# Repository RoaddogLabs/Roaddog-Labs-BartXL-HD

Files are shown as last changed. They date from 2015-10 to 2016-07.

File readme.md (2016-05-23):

## Roaddog Labs Bart Pro XL
## 
This is the Roaddog Bart XL 3D printer. This machine is a larger build
based on a mashup implemented from several designs including original
designs.  

####This machine is available in two variants

#####Bart Pro XL-LC is a lower cost version and a good upgrade platform for those with a Prusa i3 or Rework i3 variant to upgrade to a better frame and larger build area.  The LC variant uses M8 X and Z smooth rods and M5 threaded rod for the Z drive screw.  The LC uses Rework i3 printed parts.

The Bart Pro XL-LC version is frozen.  The current version is the Bart Pro XL-HD.  There will be no more work on this version but feel free to fork it and do with it as you wish.

#####Bart Pro XL-HD uses high performance lead screws, M10 precision shaft on all axis, high temp hot end suitable to 400*C, auto bed probe (bed leveling), silcone bed heater, MIC 6 precision aluminum print surface with PEI.

### This is a pre release version
### 
The current version is a pre release.  While the machine is functional
and works well, it's still very much a work in progress.  A set of pre release docs are at http://roaddoglabs.io/wiki/Roaddog_Labs_Bart_Pro_XL

Pull requests are welcome and encouraged.

#### Roaddog Labs Bart Pro XL-HD Specs ####

| Feature | Bart Pro XL-HD |
|---|---|
| Base and Frame | Full melamine frame, printed parts, latest design for maximum stability and print speeds |
| Build Envelope | 360 mm x 240 mm x 200 mm |
| Resolution (printable layer thickness) | low res .3 mm; normal res .2 mm; hi res .1 mm; extra hi res .06 mm |
| Filament Diameter | 1.75 |
| Max Printing Temp | 248&#176; C with E3D Lite v6; 300&#176; C with E3D full v6 with thermistor, 400&#176; C with optional thermocouple |
| Compatible Materials | With E3D v6, any printable material to 400&#176; C with E3D v6 and thermocouple.  With E3D Lite v6 more than 15 types including PLA, ABS, Laywoo-D, HIPS, carbon fiber reinforced PLA, flexible filament, conductive PLA |
| Nozzle Size | .4 mm standard, user upgradable to a variety of sizes |
| Heated Bed | Polyimide heater, 24 volt with aluminum heat spreader |
| Print Surface |0.125" 6061-T6 aluminum |
| Extruder | Bart Direct Drive MK7, low profile, reduced weight and mass, optional E3D Titan or Bondtech QR extruder |
| Bed Tilt Compensation | Belt tilt compensation, also called auto bed leveling or tramming via an inductive sensor |
|Electronics | Mini Rambo configured for Bart Pro XL with Marlin firmware |
| Power Supply | 24 volts, 400 watts compact form factor |
| X Axis Motion | GT2 belt and pulley;  10 mm precision  bearings and chromed, hardened rods |
| Y Axis Motion | GT2 belt and pulley;  10 mm precision  bearings and chromed, hardened rods |
| Z Axis Motion | TR8 precision lead screw and nut; 10 mm precision bearings and chromed, hardened rods |
| Average Speeds | 100 mm/s (stock extruder, perimeters based on average tune) |
| Machine Footprint | 512 mm x 470 mm x 400 mm |
| Display/SD Card Reader | Full graphic LCD display and SD card reader for standalone operation |
| Optional Wireless and Print Server | User installed optional printing over Wifi and dedicated print server using Octoprint and a Raspberry Pi |

####License and Credits

Original designs from Roaddog Labs Ltd are released per the
Open Source Hardware Association guidelines for open source hardware at
http://www.oshwa.org/definition/.

Material specific to the Bart components and documentation that is not
derived from other sources are released under the Creative Commons
Attribution 4.0 International license.

Where applicable, the license of any derived work will be posted as
well.

The original Prusa i3 single plate files
(https://github.com/josefprusa/Prusa3) from Josef Prusa licensed under
GPL v3.

The original i3 Rework
(https://github.com/eMotion-Tech/Prusai3_EINSTEIN_Reworked) printed
parts files from eMotion-Tech are released under GPL 2.0.

The original i3 Hephestos files
(https://github.com/bq/prusa-i3-hephestos/) from bq Department of
Innovation and Robotics are licensed under Creative Commons Attribution
4.0 Sharealike International.

The Graber i3(https://github.com/sgraber/Graber) is licensed under GPL
v3.0.

The original modified i3 X idler with adjustable belt tensioner from
ramkam (http://www.thingiverse.com/thing:393870) licensed under Creative
Commons Atribution-Sharealike, no version stated.

Marlin firmware (https://github.com/MarlinFirmware/Marlin) from Erik van
der Zalm licensed under GPL, no version stated.

The original direct drive extruder for Wilson/i3
(http://www.thingiverse.com/thing:501755) from mrice licensed under
Creative Commons Attribution- Share Alike license, no version stated.

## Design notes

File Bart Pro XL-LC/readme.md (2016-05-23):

## Roaddog Labs Bart Pro XL-LC
## 
This is a Roaddog Bart XL-LC 3D printer. This machine is a larger build
based on a mashup implemented from several designs including original
designs.  Original designs from Roaddog Labs Ltd are released per the
Open Source Hardware Association guidelines for open source hardware at
http://www.oshwa.org/definition/.

#####Bart Pro XL-LC is a lower cost version and a good upgrade platform for those with a Prusa i3 or Rework i3 variant to upgrade to a better frame and larger build area.  The LC variant uses M8 X and Z smooth rods and M5 threaded rod for the Z drive screw.  The LC uses Rework i3 printed parts.

This design is a legacy design and is frozen.  Feel free to fork it and add to it as you would like.

#### Roaddog Labs Bart Pro XL-LC Specs ####

| Feature | Bart Pro XL |
|---|---|
| Base and Frame | Full melamine frame, printed parts, latest design for maximum stability and print speeds |
| Build Envelope | 360 mm x 240 mm x 200 mm |
| Resolution (printable layer thickness) | low res .3 mm; normal res .2 mm; hi res .1 mm; extra hi res .06 mm |
| Filament Diameter | 1.75 |
| Max Printing Temp | 248&#176; C with E3D Lite v6; 300&#176; C with E3D full v6 with thermistor, 400&#176; C with optional thermocouple |
| Compatible Materials | With E3D v6, any printable material to 400&#176; C with E3D v6 and thermocouple.  With E3D Lite v6 more than 15 types including PLA, ABS, Laywoo-D, HIPS, carbon fiber reinforced PLA, flexible filament, conductive PLA |
| Nozzle Size | .4 mm standard, user upgradable to a variety of sizes |
| Heated Bed | Polyimide heater, 24 volt with aluminum heat spreader |
| Print Surface | 3mm borosilicate glass |
| Extruder | Bart Direct Drive MK7, low profile, reduced weight and mass |
|Electronics | Mini Rambo configured for Bart Pro XL with Marlin firmware |
| Power Supply | 24 volts, 400 watts compact form factor |
| X Axis Motion | GT2 belt and pulley;  8 mm precision  bearings and chromed, hardened rods |
| Y Axis Motion | GT2 belt and pulley;  10 mm precision  bearings and chromed, hardened rods |
| Z Axis Motion | M5 threaded rod drive screw and nut; 8 mm precision bearings and chromed, hardened rods |
| Average Speeds | 70 mm/s (stock extruder, perimeters based on average tune) |
| Machine Footprint | 512 mm x 470 mm x 400 mm |
| Display/SD Card Reader | Full graphic LCD display and SD card reader for standalone operation |
| Optional Wireless and Print Server | User installed optional printing over Wifi and dedicated print server using Octoprint and a Raspberry Pi |

####License and Credits
Material specific to the Bart components and documentation that is not
derived from other sources are released under the Creative Commons
Attribution 4.0 International license.

Where applicable, the license of any derived work will be posted as
well.

The original Prusa i3 single plate files
(https://github.com/josefprusa/Prusa3) from Josef Prusa licensed under
GPL v3.

The original i3 Rework
(https://github.com/eMotion-Tech/Prusai3_EINSTEIN_Reworked) printed
parts files from eMotion-Tech are released under GPL 2.0.

The original i3 Hephestos files
(https://github.com/bq/prusa-i3-hephestos/) from bq Department of
Innovation and Robotics are licensed under Creative Commons Attribution
4.0 Sharealike International.

The Graber i3(https://github.com/sgraber/Graber) is licensed under GPL
v3.0.

The original modified i3 X idler with adjustable belt tensioner from
ramkam (http://www.thingiverse.com/thing:393870) licensed under Creative
Commons Atribution-Sharealike, no version stated.

Marlin firmware (https://github.com/MarlinFirmware/Marlin) from Erik van
der Zalm licensed under GPL, no version stated.

The original direct drive extruder for Wilson/i3
(http://www.thingiverse.com/thing:501755) from mrice licensed under
Creative Commons Attribution- Share Alike license, no version stated.

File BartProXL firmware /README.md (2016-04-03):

### Roaddog Labs Bart Pro XL Firmware
### 
__Not for production use – use with caution!__

This fork is configured specifically for the Roaddog Labs Pro XL.  It's
currently based on Marlin 1.1.0-RC3 that was pushed 01 Dec, 2015.  This build is configured for a Mini Rambo controller using 360 mm x 240 mm print bed and Reprap Discount GLCD display

This build defaults to an induction probe in place of a mechanical Z end stop. The file [Configuration_mechanical_z.txt](./Bart_Pro_XL/Configuration_mechanical_z.txt) contains the settings for using a mechanical end stop in the A position.  To use this configuration rename the file to Configuration.h  and build the firmware.

The [original README.md](Orig_README.md) from the fork.

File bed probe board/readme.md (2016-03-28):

This is the voltage divider circuit and board layout for the Roaddog Labs Bart Pro XL.  It takes a 24 volt input and reduces the switch output to 5 volts for triggering the MCU on the printer.

This is pre release, not for production.

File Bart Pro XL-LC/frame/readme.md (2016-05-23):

## Roaddog Labs Bart Pro XL-LC
## 

Cut the following frame parts

* 2 x bart pro xl-lc side
* 2 x bart pro xl-lc z motor mount
* 2 x bart pro xl-lc z motor support
* 2 x bart pro xl-lc z top rod stop
* 2 x bart pro xl-lc y idler bearing mount
* 2 x bart pro xl-lc y belt holder

* 1 x bart pro xl-lc base 
* 1 x bart pro xl-lc print bed
* 1 x bart pro xl-lc top cross
* 1 x bart pro xl-lc y endstop bracket
* 1 x bart pro xl-lc z frame
* 1 x bart xl-lc end front
* 1 x bart xl-lc end rear

####License and Credits
Material specific to the Bart components and documentation that is not
derived from other sources are released under the Creative Commons
Attribution 4.0 International license.

Where applicable, the license of any derived work will be posted as
well.

The original Prusa i3 single plate files
(https://github.com/josefprusa/Prusa3) from Josef Prusa licensed under
GPL v3.

The original i3 Rework
(https://github.com/eMotion-Tech/Prusai3_EINSTEIN_Reworked) printed
parts files from eMotion-Tech are released under GPL 2.0.

The original i3 Hephestos files
(https://github.com/bq/prusa-i3-hephestos/) from bq Department of
Innovation and Robotics are licensed under Creative Commons Attribution
4.0 Sharealike International.

The Graber i3(https://github.com/sgraber/Graber) is licensed under GPL
v3.0.

The original modified i3 X idler with adjustable belt tensioner from
ramkam (http://www.thingiverse.com/thing:393870) licensed under Creative
Commons Atribution-Sharealike, no version stated.

Marlin firmware (https://github.com/MarlinFirmware/Marlin) from Erik van
der Zalm licensed under GPL, no version stated.

The original direct drive extruder for Wilson/i3
(http://www.thingiverse.com/thing:501755) from mrice licensed under
Creative Commons Attribution- Share Alike license, no version stated.

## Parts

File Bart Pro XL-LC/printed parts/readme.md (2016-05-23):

## Roaddog Labs Bart Pro XL-LC
## 

Print the following parts

* 1 x bart pro xl-lc y motor mount
* 8 x bart pro xl-lc Y bearing mount
* 3 x bart pro xl-lc y clip
* 1 x bart pro xl-lc y end stop bracket

* 1 x bart pro xl-lc X motor end
* 1 x bart pro xl-lc X idler end
* 1 x bart pro xl-lc x belt  idler  
* 1 x bart pro xl-lc x endstop bracket
* 1 x bart pro xl-lc x endstop block
* 1 x bart pro xl-lc x carriage

* 1 x bart pro xl-lc z endstop bracket
* 1 x bart pro xl-lc extruder
* 1 x bart pro xl-lc extruder fan duct

####License and Credits
Material specific to the Bart components and documentation that is not
derived from other sources are released under the Creative Commons
Attribution 4.0 International license.

Where applicable, the license of any derived work will be posted as
well.

The original Prusa i3 single plate files
(https://github.com/josefprusa/Prusa3) from Josef Prusa licensed under
GPL v3.

The original i3 Rework
(https://github.com/eMotion-Tech/Prusai3_EINSTEIN_Reworked) printed
parts files from eMotion-Tech are released under GPL 2.0.

The original i3 Hephestos files
(https://github.com/bq/prusa-i3-hephestos/) from bq Department of
Innovation and Robotics are licensed under Creative Commons Attribution
4.0 Sharealike International.

The Graber i3(https://github.com/sgraber/Graber) is licensed under GPL
v3.0.

The original modified i3 X idler with adjustable belt tensioner from
ramkam (http://www.thingiverse.com/thing:393870) licensed under Creative
Commons Atribution-Sharealike, no version stated.

Marlin firmware (https://github.com/MarlinFirmware/Marlin) from Erik van
der Zalm licensed under GPL, no version stated.

The original direct drive extruder for Wilson/i3
(http://www.thingiverse.com/thing:501755) from mrice licensed under
Creative Commons Attribution- Share Alike license, no version stated.

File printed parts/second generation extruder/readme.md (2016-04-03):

Roaddog Labs Ltd Bart Pro XL 2nd Gen Extruder

This is a prototype 2nd generation extruder.  

Updates include 

provisions for the push connector in the E3D hot end

two screw JHead style mount

This is still experimental pull requests and suggestions are encouraged.

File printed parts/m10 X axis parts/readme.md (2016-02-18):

Roaddog Labs Ltd Bart Pro XL LM10UU X axis

This is a prototype X axis using LM10UU bearings and M10 shafts.  This is still experimental pull requests and suggestions are encouraged.

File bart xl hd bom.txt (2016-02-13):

**** not released for production ****
**** copied from Bart, needs audit ****

Bill of Materials
Roaddog Labs Ltd Bart XL HD
file released under Creative Commons
Attribution 4.0 International license.

Frame

2 x 24" x18" 1/4" melamine, black or white, two sides laminated

Rods

2 x M5-.8 x 300 mm threaded rod, Z axis lead screws

2 x M8 x 318 mm smooth rod, (320 mm will work also)

2 x M8 x 368 mm smooth rod 

2 x M10 x 511 mm smooth rod 

Bearings

4 x LM10UU linear bearings
7 x LM8UU linear bearings
3 x 624ZZ bearings

Printed Parts

4 x Y clips
1 x Y motor bracket
4 x Y bearing mounts (each mount is two pieces)

1 x X carriage
1 x x endstop block
1 x X end motor
1 x X end idler
1 x X idler

1 x extruder body 
1 x extruder idler
1 x hot end mounting clip
1 x fan duct

1 x z endstop bracket

Misc Hardware

1 x M7 hobbed drive gear, filament drive gear
2 x GT2 pulley, 20 teeth, 5 mm diameter mounting hole
2 meters GT2 belt

4 x rubber feet

2 x 3/16" ID poly tubing, 1" long each, coupler tubing 

1 x 214 x 200 borosilicate glass print bed

4 x small binder clips for glass bed

4 bed springs (get final specs)
2 extruder springs (get final specs)

Fasteners  (totals rounded up from final prototype, shcs count not exact)

50 x 6-32 square nut, frame
50 x 6-32 x 5/8" pan head machine screws, frame
4 x 6-32 x 1/2" pan head machine screws, frame
4 x #6 flat washer, frame

20 x  M3 x 10 mm shcs, motor mounts, endstop screws
25 x  M3 x 12 mm shcs, motor/Z endstop bracket mounting, feet mounting
05 x  M3 x 14 mm shcs,
05 x  M3 x 16 mm shcs,
08 x  M3 x 25 mm shcs,
06 x  M3 x 30 mm shcs, 
02 x  M3 x 35 mm shcs,
02 x  M3 x 50 mm shcs,

55 x  M3 washer
30 x  M3 hex nut
12 x  M3 nyloc nut

07 x  M4 x 20 shcs extruder mount, extruder idler
01 x  M4 x 30 shcs Y idler bearing

06 x  M4 hex nut
10 x  M4 flat washer
03 x  M4 nyloc nut

02 x  M5 nut

4 x nylon spacers (snap fit does not fit iduino/Arduino pcb mounting hole)

Electronics

1 x Mini Rambo control board

1 x 40x40x10 12 volt axial fan

5 x NEMA 17 stepper motors, recommend 76 oz/in holding torque

1 x 400 watt, 24 volt PSU

1 x kapton tape heating pad

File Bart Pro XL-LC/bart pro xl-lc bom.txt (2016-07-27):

Bill of Materials
Roaddog Labs Ltd Bart Pro XL-LC
file released under Creative Commons
Attribution 4.0 International license.

Frame

2 x 24" x18" 1/4" melamine, two sides laminated

Rods

2 x M5-.8 x 300 mm threaded rod, Z axis drive screws

2 x M8 x 318 mm smooth rod

2 x M8 x 370 mm smooth rod 

2 x M10 x 511 mm smooth rod 

Bearings

4 x LM10UU linear bearings
8 x LM8UU linear bearings
3 x 624ZZ bearings

Printed Parts

2 x Y clips
1 x Y clip/end stop bracket
1 x Y motor bracket
4 x Y bearing mounts (each mount is two pieces)

1 x X carriage
1 x x endstop block
1 x X end motor
1 x X end idler
1 x X idler

1 x extruder body 
1 x extruder idler
1 x hot end mounting clip
1 x fan duct

1 x z endstop bracket

Misc Hardware

1 x M7 hobbed drive gear, filament drive gear
2 x GT2 pulley, 20 teeth, 5 mm diameter mounting hole
2 meters GT2 belt

4 x rubber feet

2 x 3/16" ID poly tubing, 1" long each, coupler tubing 

1 x 214 x 200 borosilicate glass print bed

4 x small binder clips for glass bed

4 x bed springs (get final specs)
2 x extruder springs (get final specs)

1 x aluminum print bed sheet .125 thick, 360 mm x 240 mm 6061-T6 

1 x borosilicate glass, 3 mm thick 360 mm x 240 mm 

Fasteners 

50 x 6-32 square nut, frame
50 x 6-32 x 5/8" pan head machine screws, frame
4 x 6-32 x 1/2" pan head machine screws, frame
4 x #6 flat washer, frame

20 x  M3 x 10 mm shcs, motor mounts, endstop screws
25 x  M3 x 12 mm shcs, motor/Z endstop bracket mounting, feet mounting
05 x  M3 x 14 mm shcs,
05 x  M3 x 16 mm shcs,
08 x  M3 x 25 mm shcs,
06 x  M3 x 30 mm shcs, 
02 x  M3 x 35 mm shcs,
02 x  M3 x 50 mm shcs,

55 x  M3 washer
30 x  M3 hex nut
12 x  M3 nyloc nut

07 x  M4 x 20 shcs extruder mount, extruder idler
01 x  M4 x 30 shcs Y idler bearing

06 x  M4 hex nut
10 x  M4 flat washer
03 x  M4 nyloc nut

02 x  M5 nut

4 x nylon spacers (snap fit does not fit iduino/Arduino pcb mounting hole)

Electronics

1 x Mini Rambo control board

1 x E3D v6 hot end kit

1 x 40x40x10 24 volt axial fan

5 x NEMA 17 stepper motors, recommend 76 oz/in holding torque

1 x 400 watt, 24 volt PSU

1 x kapton tape heating pad

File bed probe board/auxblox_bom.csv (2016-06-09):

CN1,CN2 | S1011EC-40-ND | 2
R1 | 985-1300-1-ND | 1
R2 | 985-1311-1-ND | 1

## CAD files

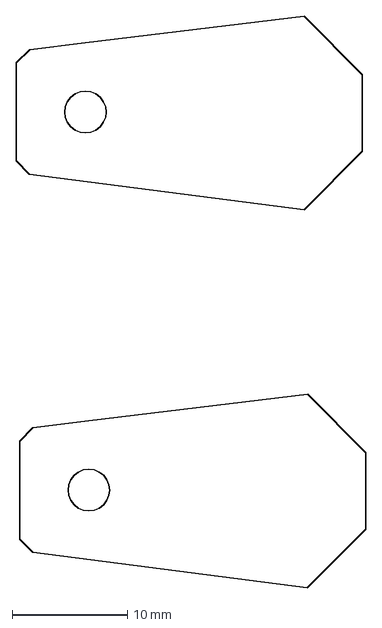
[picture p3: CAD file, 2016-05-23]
Bart Pro XL-LC/frame/bart pro xl-lc z top rod stop.dxf
30.3 x 49.6 mm

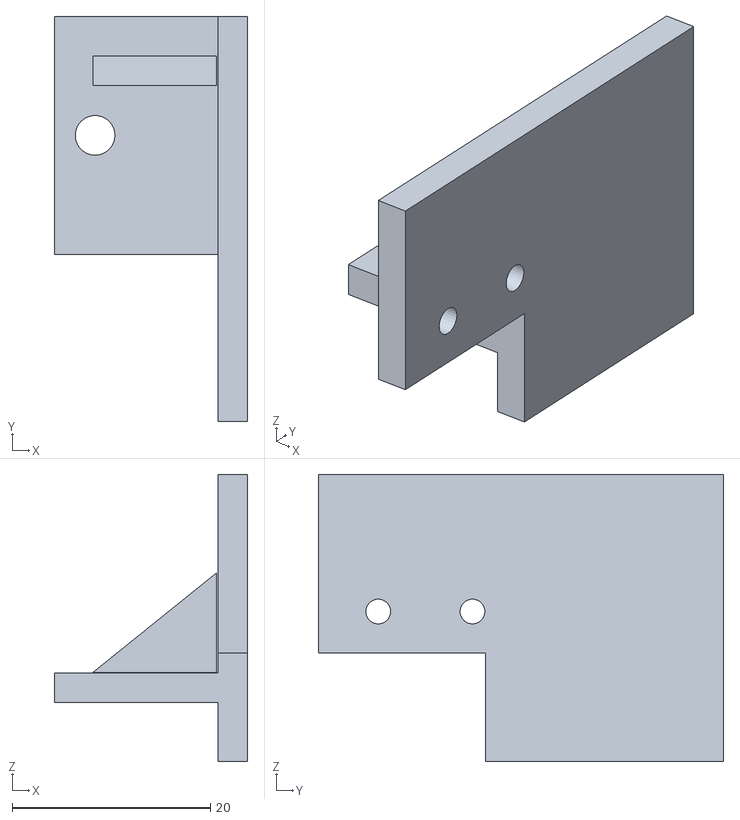
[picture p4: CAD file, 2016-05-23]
Bart Pro XL-LC/printed parts/bart pro xl-lc y end stop bracket.stl
19.5 x 40.9 x 28.9

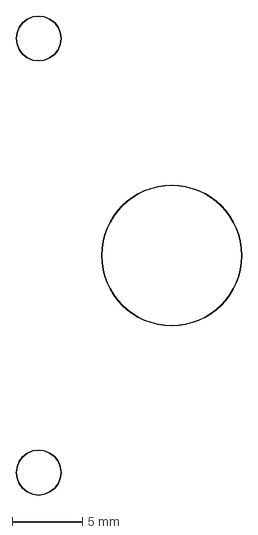
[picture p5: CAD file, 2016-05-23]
frame/bart pro xl m10 bottom Z rod guide spacing.dxf
16.1 x 34.2 mm

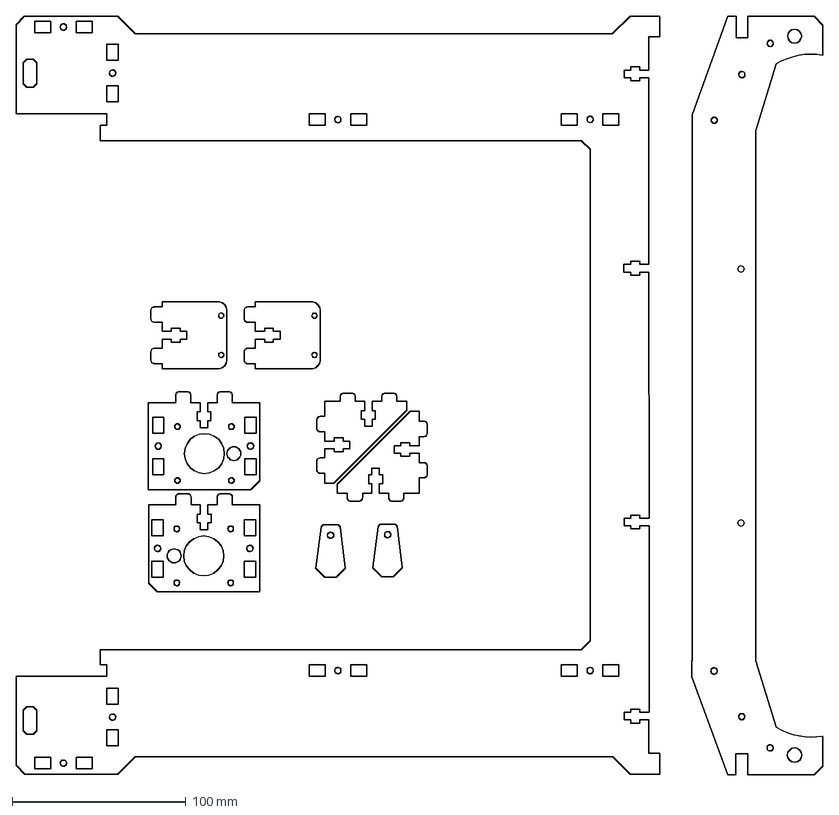
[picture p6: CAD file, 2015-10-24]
frame/v1 frame parts/bart xl one piece top cross and frame v2.dxf
463.9 x 436.3 mm

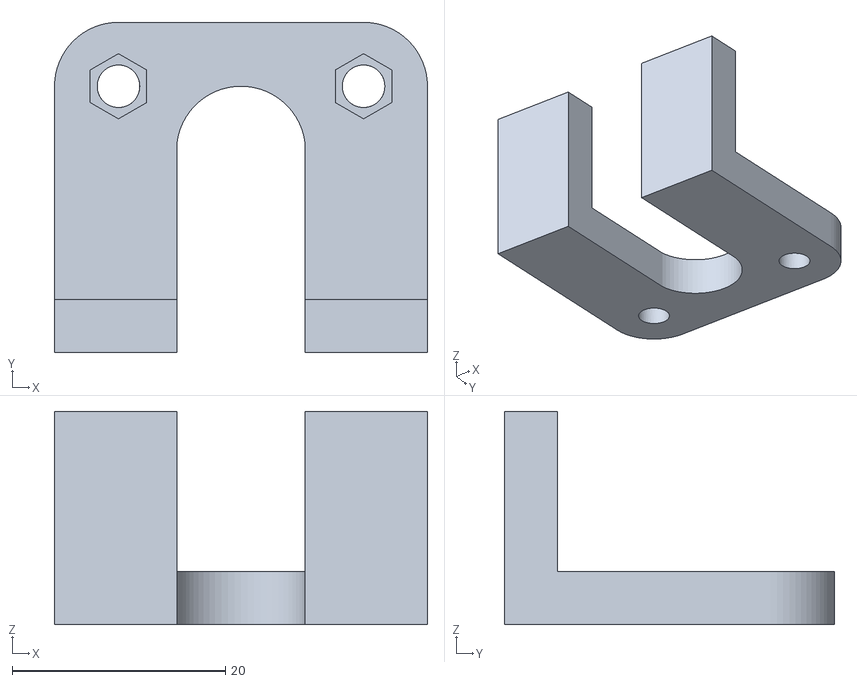
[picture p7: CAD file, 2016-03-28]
printed parts/bart pro xl bed probe bracket.stl
35.0 x 31.0 x 20.0

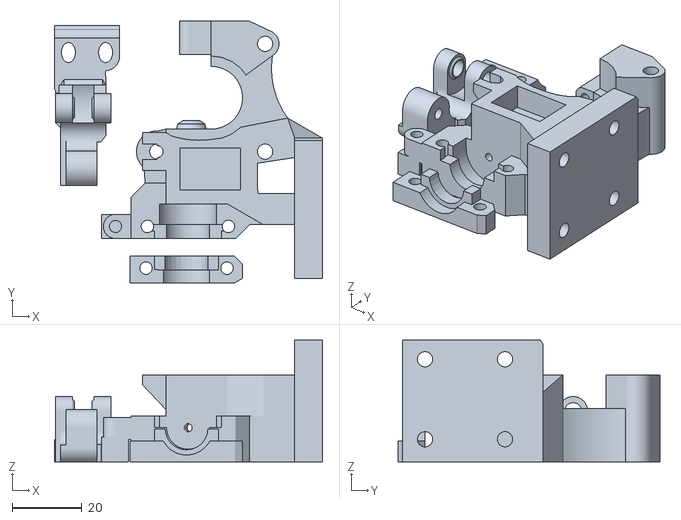
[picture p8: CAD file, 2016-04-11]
printed parts/dual extruder/extruder motor on right.stl
77.1 x 75.2 x 35.0

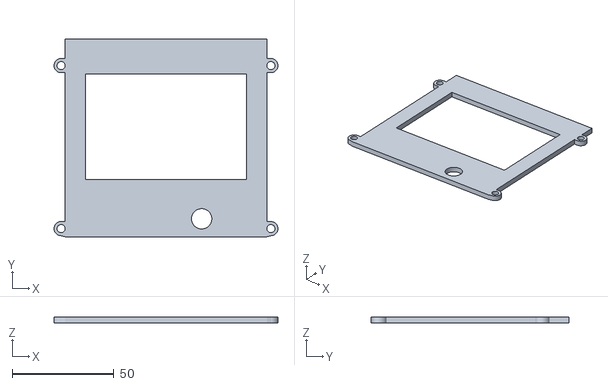
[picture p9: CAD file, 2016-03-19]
printed parts/glcd case/bart pro xl glcd case face.stl
110.0 x 97.0 x 3.00

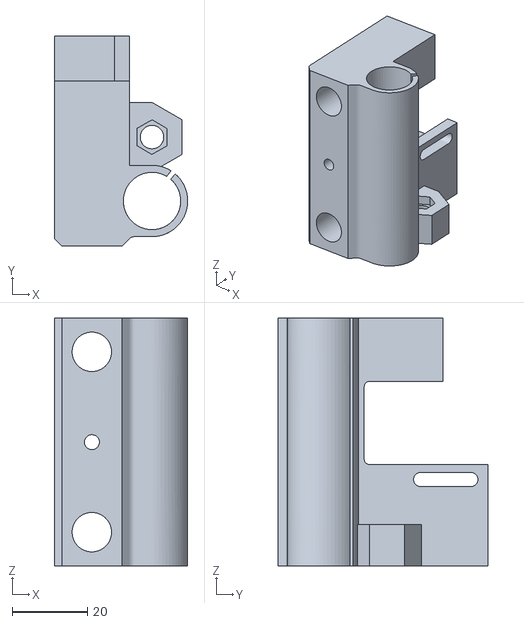
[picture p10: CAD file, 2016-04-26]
printed parts/m10 X axis parts/bart pro xl x idler end v26.stl
35.5 x 56.0 x 66.0

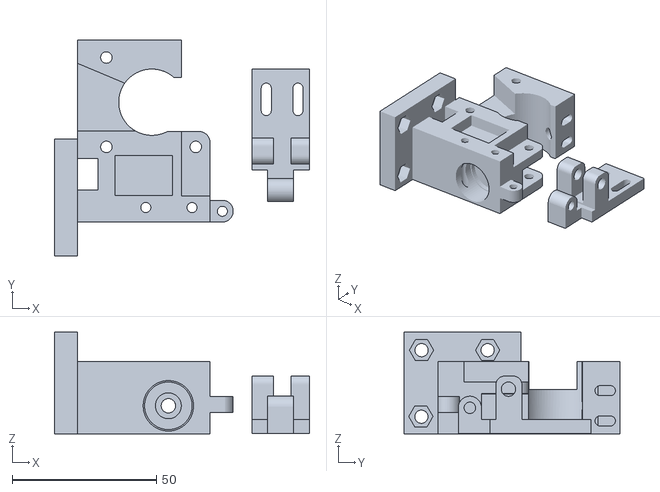
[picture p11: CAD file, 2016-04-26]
printed parts/second generation extruder/bart pro xl 2nd gen extruder v9.stl
88.5 x 74.8 x 35.2

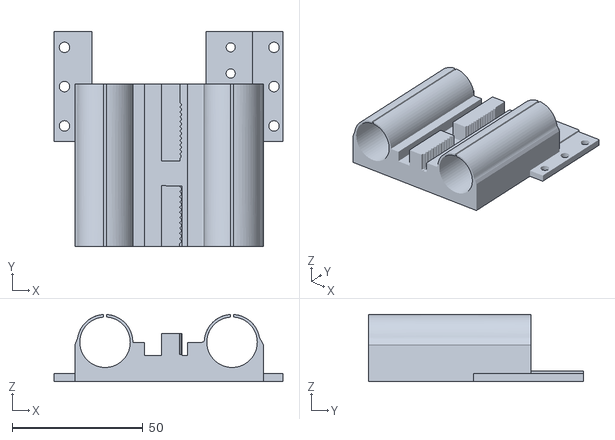
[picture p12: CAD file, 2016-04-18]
printed parts/titan x carriage-bracket/bart pro xl titan x carriage.stl
87.4 x 82.0 x 25.6

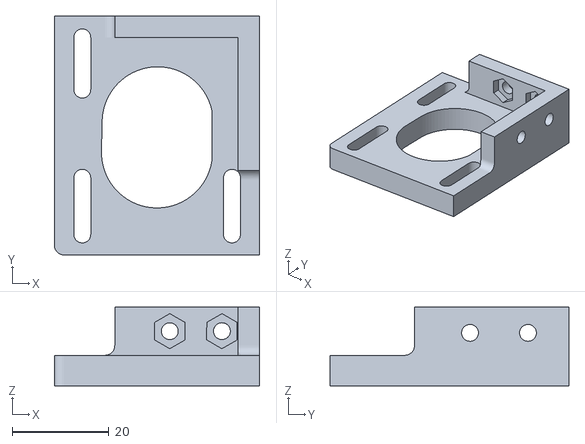
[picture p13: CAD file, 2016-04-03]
Bart Pro XL-LC/printed parts/bart pro xl-lc y motor mount.stl
42.5 x 49.5 x 16.4

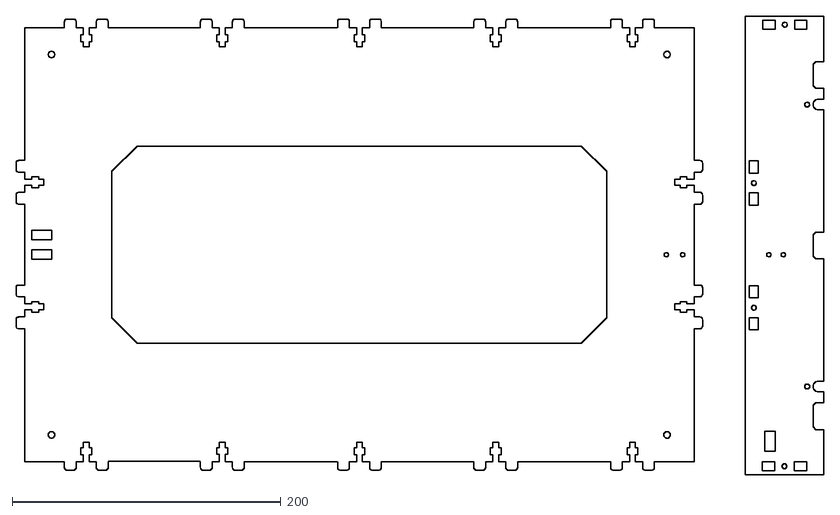
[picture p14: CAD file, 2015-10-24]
frame/v1 frame parts/bart xl base and rear panel.dxf
601.7 x 341.5

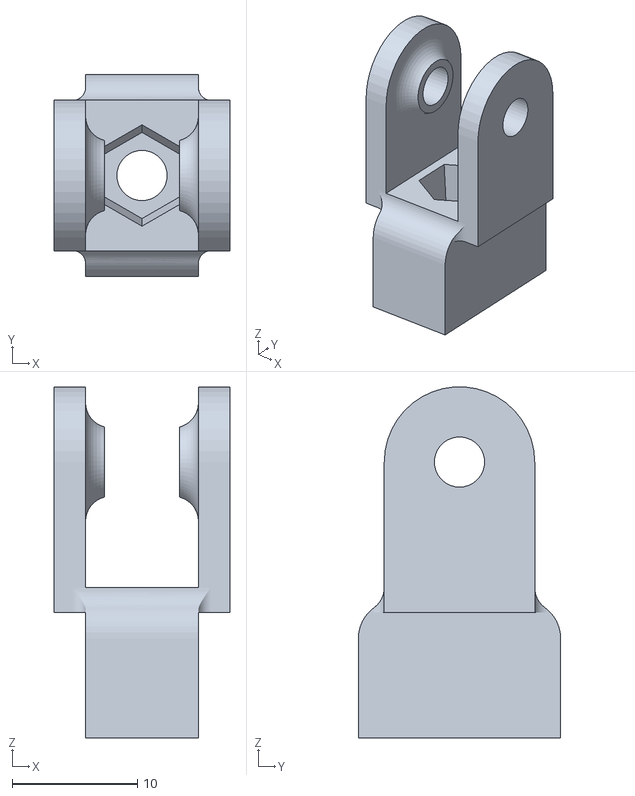
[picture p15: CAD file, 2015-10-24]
printed parts/bart X end idler.stl
14.0 x 16.1 x 28.0

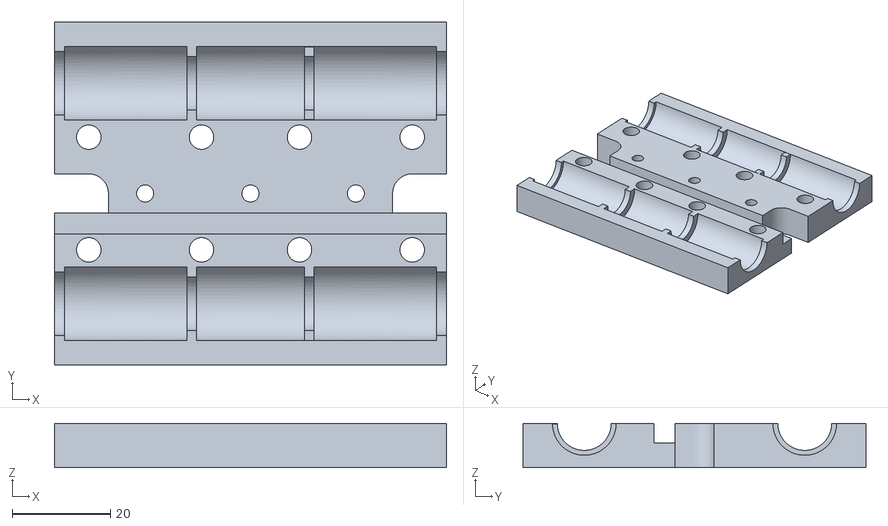
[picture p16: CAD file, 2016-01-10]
printed parts/dual extruder/bart xl dual extruder x carriage lm8uu front.stl
80.0 x 70.0 x 9.00

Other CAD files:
Bart Pro XL-LC/frame/bart pro xl-lc base .dxf
printed parts/glcd case/bart pro xl glcd case base.stl
printed parts/m10 X axis parts/bart pro xl x idler.stl
Bart Pro XL-LC/frame/bart pro xl-lc print bed.dxf
Bart Pro XL-LC/frame/bart pro xl-lc side.dxf
Bart Pro XL-LC/frame/bart pro xl-lc top cross.dxf
Bart Pro XL-LC/frame/bart pro xl-lc y belt holder.dxf
Bart Pro XL-LC/frame/bart pro xl-lc y endstop bracket.dxf
Bart Pro XL-LC/frame/bart pro xl-lc y idler bearing mount.dxf
Bart Pro XL-LC/frame/bart pro xl-lc z frame.dxf
Bart Pro XL-LC/frame/bart pro xl-lc z motor mount.dxf
Bart Pro XL-LC/frame/bart pro xl-lc z motor support.dxf
Bart Pro XL-LC/frame/bart xl-lc end front.dxf
Bart Pro XL-LC/frame/bart xl-lc end rear.dxf
Bart Pro XL-LC/printed parts/bart pro xl-lc X idler end.stl
Bart Pro XL-LC/printed parts/bart pro xl-lc X motor end.stl
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

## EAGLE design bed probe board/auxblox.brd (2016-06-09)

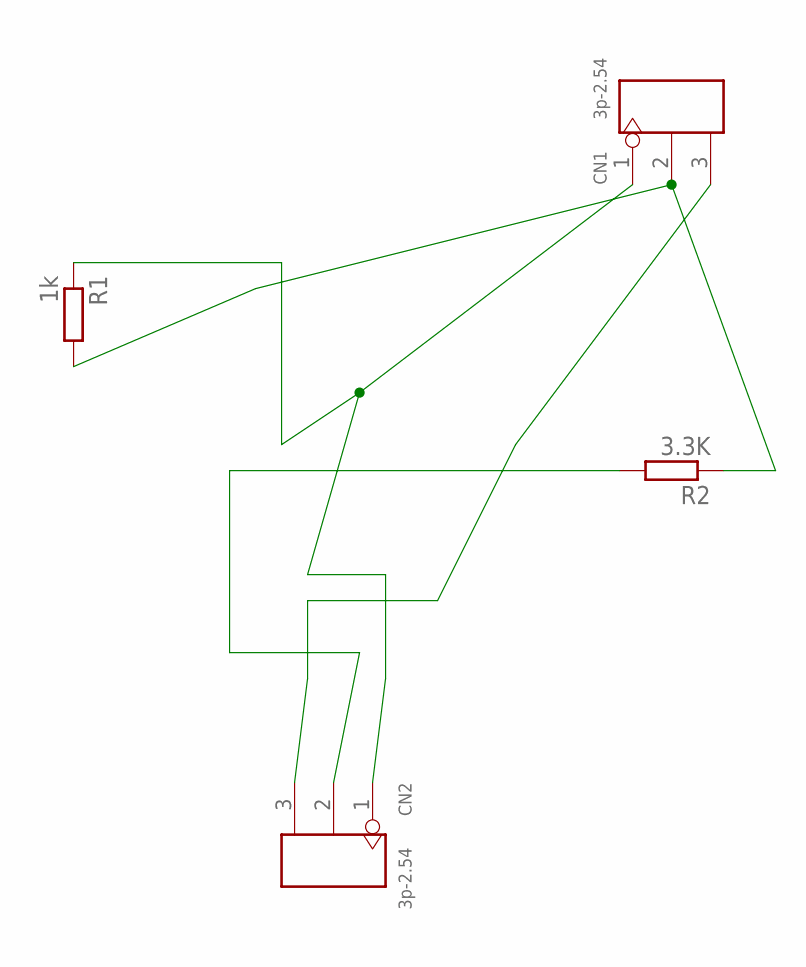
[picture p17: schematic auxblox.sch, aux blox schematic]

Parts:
CN1, CN2: 3p-2.54; H3-2.54
R1: 1k; R0805
R2: 3.3K; R0805

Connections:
unnamed: CN1.3, CN2.3
unnamed: CN2.2, R2.2
unnamed: CN1.1, CN2.1, R1.1
unnamed: CN1.2, R1.2, R2.1

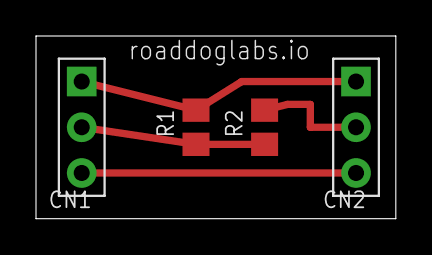
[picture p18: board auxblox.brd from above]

Board: 2 copper layers, 20.0 x 10.1 mm, 4 parts (0 on the bottom side), 4 nets.

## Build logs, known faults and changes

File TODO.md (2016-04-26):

##To Do list for outstanding issues/feature enhancements/ etc

- [x] validate Titan mounts

     - [x] print titan mount prototypes
     - [ ] test titan mounts

- [ ] remove m8 X axis parts from default branch

- [x] fix thermal runaway false trigger on bed #38
     - [x] removed trigger
     - [ ] fully fix runaway issue
- [x] resolve #42 #43

- [ ] print and validate latest 2nd gen extruder
- [x] set extruder body flat on bed for printing

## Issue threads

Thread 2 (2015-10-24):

fix X carriage rear screw interference with main frame

RoaddogLabs, 2015-10-24:

Closed 2015-12-11.

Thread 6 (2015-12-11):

change Z and X endstops to switch only

RoaddogLabs, 2015-12-11:
change the switches so they use switches only instead of pcb style switches

RoaddogLabs, 2015-12-23:
design complete, needs prototypes printed and tested

Closed 2016-01-10.

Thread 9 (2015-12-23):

design display mount

RoaddogLabs, 2015-12-23:
needs to access sd card slot on right hand side
explore using front right
mindful of the cable lengths

Closed 2016-02-19.

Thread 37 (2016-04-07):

rc5 changes x direction

RoaddogLabs, 2016-04-07:
build of RC5 changes the X dir, temporarily setting the motor dir to compensate.

I mean really guys.  Really...

RoaddogLabs, 2016-04-07:
it appears the implementation of the logic for the end stops has changed in this rev

auto bed leveling implementation has been changed as well, breaking it from RC3

branch is unusable even as a beta.

alpha status, several broken or incompletely implemented features

Closed 2016-04-07.

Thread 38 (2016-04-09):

false bed thermal runaway alarms

RoaddogLabs, 2016-04-09:
bed heating triggering false runaway alerts
disable until solved

RoaddogLabs, 2016-04-30:
determine different timeout interval as not to trigger this condition

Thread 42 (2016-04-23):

x end revisions

RoaddogLabs, 2016-04-23:
- [x] add thicker linear bearing wall on both parts

- [x] x belt idler bolt clearance

- [x] redesign x end stop bracket, move switch to x carriage

this issue also references #43

RoaddogLabs, 2016-04-26:
works great

Closed 2016-04-26.

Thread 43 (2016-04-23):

Z motor mount revision

RoaddogLabs, 2016-04-23:
move Z rod center line out 5 mm from frame for clearance

RoaddogLabs, 2016-04-23:
parts modified, test cuts and fit

RoaddogLabs, 2016-04-26:
works great

Closed 2016-04-26.

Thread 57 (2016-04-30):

fix z probe homing lift as not to trigger max travel at max z height

RoaddogLabs, 2016-04-30:
when z is at max height homing z will fail due to z needing to lift 10 mm to begin home

change config to eliminate this

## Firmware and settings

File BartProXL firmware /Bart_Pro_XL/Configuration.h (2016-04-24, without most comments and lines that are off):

#define CONFIGURATION_H
#include "boards.h"
#include "macros.h"
#if ENABLED(USE_AUTOMATIC_VERSIONING)
  #include "_Version.h"
#else
  #include "Default_Version.h"
#endif
#define STRING_CONFIG_H_AUTHOR "(RoaddogLabsLtd, BartProXL)" // Who made the changes.
#define SHOW_BOOTSCREEN
#define STRING_SPLASH_LINE1 SHORT_BUILD_VERSION // will be shown during bootup in line 1
#define SERIAL_PORT 0
#define BAUDRATE 250000
  #define MOTHERBOARD BOARD_MINIRAMBO
#define CUSTOM_MACHINE_NAME "Bart Pro XL"
#define EXTRUDERS 1
#define POWER_SUPPLY 1
#define TEMP_SENSOR_0 5
#define TEMP_SENSOR_1 0
#define TEMP_SENSOR_2 0
#define TEMP_SENSOR_3 0
#define TEMP_SENSOR_BED 60
#define MAX_REDUNDANT_TEMP_SENSOR_DIFF 10
#define TEMP_RESIDENCY_TIME 10  // (seconds)
#define TEMP_HYSTERESIS 3       // (degC) range of +/- temperatures considered "close" to the target one
#define TEMP_WINDOW     1       // (degC) Window around target to start the residency timer x degC early.
#define HEATER_0_MINTEMP 5
#define HEATER_1_MINTEMP 5
#define HEATER_2_MINTEMP 5
#define HEATER_3_MINTEMP 5
#define BED_MINTEMP 5
#define HEATER_0_MAXTEMP 275
#define HEATER_1_MAXTEMP 275
#define HEATER_2_MAXTEMP 275
#define HEATER_3_MAXTEMP 275
#define BED_MAXTEMP 150
#define PIDTEMP
#define BANG_MAX 255 // limits current to nozzle while in bang-bang mode; 255=full current
#define PID_MAX BANG_MAX // limits current to nozzle while PID is active (see PID_FUNCTIONAL_RANGE below); 255=full current
  #define PID_FUNCTIONAL_RANGE 10 // If the temperature difference between the target temperature and the actual temperature
  #define PID_INTEGRAL_DRIVE_MAX PID_MAX  //limit for the integral term
  #define K1 0.95 //smoothing factor within the PID
	#define  DEFAULT_Kp 15.8
    #define  DEFAULT_Ki 1.08
    #define  DEFAULT_Kd 120
#define MAX_BED_POWER 255 // limits duty cycle to bed; 255=full current
#define PREVENT_DANGEROUS_EXTRUDE
#define PREVENT_LENGTHY_EXTRUDE
#define EXTRUDE_MINTEMP 170
#define EXTRUDE_MAXLENGTH (X_MAX_LENGTH+Y_MAX_LENGTH) //prevent extrusion of very large distances.
  #define ENDSTOPPULLUP_XMAX
  #define ENDSTOPPULLUP_YMAX
  #define ENDSTOPPULLUP_ZMAX
  #define ENDSTOPPULLUP_XMIN
  #define ENDSTOPPULLUP_YMIN
const bool X_MIN_ENDSTOP_INVERTING = true; // set to true to invert the logic of the endstop.
const bool Y_MIN_ENDSTOP_INVERTING = true; // set to true to invert the logic of the endstop.
const bool Z_MIN_ENDSTOP_INVERTING = false; // set to true to invert the logic of the endstop.
const bool X_MAX_ENDSTOP_INVERTING = true; // set to true to invert the logic of the endstop.
const bool Y_MAX_ENDSTOP_INVERTING = true; // set to true to invert the logic of the endstop.
const bool Z_MAX_ENDSTOP_INVERTING = true; // set to true to invert the logic of the endstop.
const bool Z_MIN_PROBE_ENDSTOP_INVERTING = false; // set to true to invert the logic of the endstop.
#define X_ENABLE_ON 0
#define Y_ENABLE_ON 0
#define Z_ENABLE_ON 0
#define E_ENABLE_ON 0 // For all extruders
#define DISABLE_X false
#define DISABLE_Y false
#define DISABLE_Z false
#define DISABLE_E false // For all extruders
#define DISABLE_INACTIVE_EXTRUDER true //disable only inactive extruders and keep active extruder enabled
#define INVERT_X_DIR true    // Bart set to true
#define INVERT_Y_DIR false    // Bart set to false
#define INVERT_Z_DIR true     // Bart set to true
#define INVERT_E0_DIR false   // Bart MK7 direct drive motor on left set to false, motor on right set to true, Gregs Wades set to false
#define INVERT_E1_DIR false    // Bart MK7 direct drive motor on left set to false, motor on right set to true
#define INVERT_E2_DIR false   // not used for Bart
#define X_HOME_DIR 1
#define Y_HOME_DIR -1
#define Z_HOME_DIR -1
#define min_software_endstops true // If true, axis won't move to coordinates less than HOME_POS.
#define max_software_endstops true  // If true, axis won't move to coordinates greater than the defined lengths below.
#define X_MIN_POS 0
#define Y_MIN_POS 0
#define Z_MIN_POS 0
#define X_MAX_POS 240
#define Y_MAX_POS 360
#define Z_MAX_POS 200
#define AUTO_BED_LEVELING_FEATURE // Delete the comment to enable (remove // at the start of the line)
#define DEBUG_LEVELING_FEATURE
#define Z_MIN_PROBE_REPEATABILITY_TEST  // If not commented out, Z-Probe Repeatability test will be included if Auto Bed Leveling is Enabled.
    #define ABL_PROBE_PT_1_X 180
    #define ABL_PROBE_PT_1_Y 180
    #define ABL_PROBE_PT_2_X 60
    #define ABL_PROBE_PT_2_Y 20
    #define ABL_PROBE_PT_3_X 170
    #define ABL_PROBE_PT_3_Y 20
  #define X_PROBE_OFFSET_FROM_EXTRUDER  22     // Z probe to nozzle X offset: -left  +right
  #define Y_PROBE_OFFSET_FROM_EXTRUDER  0     // Z probe to nozzle Y offset: -front +behind
  #define Z_PROBE_OFFSET_FROM_EXTRUDER  -.8  // Z probe to nozzle Z offset: -below (always!)
  #define Z_RAISE_BEFORE_HOMING 4       // (in mm) Raise Z axis before homing (G28) for Z probe clearance.
  #define XY_TRAVEL_SPEED 8000         // X and Y axis travel speed between probes, in mm/min.
  #define Z_RAISE_BEFORE_PROBING 5   // How much the Z axis will be raised before traveling to the first probing point.
  #define Z_RAISE_BETWEEN_PROBINGS 5  // How much the Z axis will be raised when traveling from between next probing points.
  #define Z_RAISE_AFTER_PROBING 5    // How much the Z axis will be raised after the last probing point.
  #define Z_SAFE_HOMING   // This feature is meant to avoid Z homing with Z probe outside the bed area.
    #define Z_SAFE_HOMING_X_POINT ((X_MIN_POS + X_MAX_POS) / 2)    // X point for Z homing when homing all axis (G28).
    #define Z_SAFE_HOMING_Y_POINT ((Y_MIN_POS + Y_MAX_POS) / 2)    // Y point for Z homing when homing all axis (G28).
#define HOMING_FEEDRATE {50*60, 50*60, 4*60, 0}  // set the homing speeds (mm/min)
#define DEFAULT_AXIS_STEPS_PER_UNIT   {80,80,400,98}  // default steps per unit for T8 lead screw Bart Pro XL Bart direct drive extruder
#define DEFAULT_MAX_FEEDRATE          {300, 300, 2, 25}    // (mm/sec)
#define DEFAULT_MAX_ACCELERATION      {3000,3000,10,10000}    // X, Y, Z, E maximum start speed for accelerated moves. E default values are good for Skeinforge 40+, for older versions raise them a lot.
#define DEFAULT_ACCELERATION          3000    // X, Y, Z and E acceleration in mm/s^2 for printing moves
#define DEFAULT_RETRACT_ACCELERATION  3000    // E acceleration in mm/s^2 for retracts
#define DEFAULT_TRAVEL_ACCELERATION   3000    // X, Y, Z acceleration in mm/s^2 for travel (non printing) moves
#define DEFAULT_XYJERK                6.0    // (mm/sec)  //set from Bart default =20
#define DEFAULT_ZJERK                 0.4     // (mm/sec)
#define DEFAULT_EJERK                 5.0    // (mm/sec)
#define CUSTOM_M_CODES
    #define CUSTOM_M_CODE_SET_Z_PROBE_OFFSET 851
    #define Z_PROBE_OFFSET_RANGE_MIN -20
    #define Z_PROBE_OFFSET_RANGE_MAX 20
#define PLA_PREHEAT_HOTEND_TEMP 200
#define PLA_PREHEAT_HPB_TEMP 50
#define PLA_PREHEAT_FAN_SPEED 0   // Insert Value between 0 and 255
#define ABS_PREHEAT_HOTEND_TEMP 230
#define ABS_PREHEAT_HPB_TEMP 100
#define ABS_PREHEAT_FAN_SPEED 0   // Insert Value between 0 and 255
#define LANGUAGE_INCLUDE GENERATE_LANGUAGE_INCLUDE(en)
  #define DISPLAY_CHARSET_HD44780_JAPAN        // this is the most common hardware
#define ULTRA_LCD  //general LCD support, also 16x2
#define SDSUPPORT // Enable SD Card Support in Hardware Console
#define REPRAP_DISCOUNT_FULL_GRAPHIC_SMART_CONTROLLER
#define SOFT_PWM_SCALE 0
#define FILAMENT_SENSOR_EXTRUDER_NUM 0   //The number of the extruder that has the filament sensor (0,1,2)
#define MEASUREMENT_DELAY_CM        14   //measurement delay in cm.  This is the distance from filament sensor to middle of barrel
#define DEFAULT_NOMINAL_FILAMENT_DIA 3.00  //Enter the diameter (in mm) of the filament generally used (3.0 mm or 1.75 mm) - this is then used in the slicer software.  Used for sensor reading validation
#define MEASURED_UPPER_LIMIT         3.30  //upper limit factor used for sensor reading validation in mm
#define MEASURED_LOWER_LIMIT         1.90  //lower limit factor for sensor reading validation in mm
#define MAX_MEASUREMENT_DELAY       20     //delay buffer size in bytes (1 byte = 1cm)- limits maximum measurement delay allowable (must be larger than MEASUREMENT_DELAY_CM  and lower number saves RAM)
#define DEFAULT_MEASURED_FILAMENT_DIA  DEFAULT_NOMINAL_FILAMENT_DIA  //set measured to nominal initially
#include "Configuration_adv.h"
#include "thermistortables.h"

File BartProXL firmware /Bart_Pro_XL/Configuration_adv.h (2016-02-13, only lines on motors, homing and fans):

#define CONTROLLERFAN_PIN -1 //Pin used for the fan to cool controller (-1 to disable)
#define EXTRUDER_0_AUTO_FAN_PIN 6
#define EXTRUDER_1_AUTO_FAN_PIN -1
#define EXTRUDER_2_AUTO_FAN_PIN -1
#define EXTRUDER_3_AUTO_FAN_PIN -1
#define ENDSTOPS_ONLY_FOR_HOMING // If defined the endstops will only be used for homing
#define X_HOME_BUMP_MM 5
#define Y_HOME_BUMP_MM 5
#define Z_HOME_BUMP_MM 2
#define HOMING_BUMP_DIVISOR {2, 2, 4}  // Re-Bump Speed Divisor (Divides the Homing Feedrate)
#define MICROSTEP_MODES {16,16,16,16,16} // [1,2,4,8,16]
#define DIGIPOT_MOTOR_CURRENT {135,135,135,135,135} // Values 0-255 (RAMBO 135 = ~0.75A, 185 = ~1A)
#define DIGIPOT_I2C_MOTOR_CURRENTS {1.0, 1.0, 1.0, 1.0, 1.0, 1.0, 1.0, 1.0}

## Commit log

2015-09-11 initial commit
    initial commit
    [bart hd xl all v2.dwg, bart hd xl all.dwg, bart hd xl ends.dwg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]
2015-10-24 working proto
    woring prototype with dual extruder carriage
    [bart X end idler.stl, bart X end.stl, bart X motor end.stl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]
2015-10-24 base dual extruder Marlin config
    add base dual marlin config with larger build envelope and activated
    watchdog
    [Configuration.h, Configuration_adv.h, Menu Plans.xlsx]
2015-10-24 bed revision
    added print plate mounting holes
    extended endstop trigger
    [bart print bed v3.dxf]
2015-10-24 added extra cut parts, new top
    [bart xl one piece top cross and frame v2.dxf]
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2015-11-08 update frame parts
    update to “pro” frame, taller, more stable
    [bart pro xl top cross and frame.dxf, bart pro xl ends 10 mm rods.dxf, bart pro xl ends.dxf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]
2015-12-08 update Marlin RAMPS to Bart XL
    [Configuration.h]
2015-12-08 update bed frame to LM10uu
    [bart print bed v4 lm10uu.dxf]
2015-12-08 update Marlin 1.1.0-RC2 config & add RC3 dist
    [Configuration.h, Configuration_adv.h, Marlin Logo.dxf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]
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2015-12-25 Use Prusa's Marlin 1.0.3 for Mini Rambo
    rolled back to a build-able version of Marlin
    removed the two 1.1 RC branches
    [Configuration.h, Configuration_adv.h, Marlin Logo.dxf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]
2015-12-25 archive v1 base part
    [bart xl base and rear panel.dxf]
2015-12-25 update printed parts and source
    [bart X end idler.stl, bart Y endstop bracket-clip.stl, bart x endstop bracket plain switch v1.ipt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]
2015-12-25 set base firmware config
    [Configuration.h]
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2016-01-10 dual extruder x carriage updates
    [bart xl dual extruder x carriage lm8uu front.f3d, bart xl dual extruder x carriage either bearings rear.stl, bart xl dual extruder x carriage igus bearings fro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]
2016-02-06 release candidate firmware
    archive older versions to folder
    implement Marlin 1.1.0 RC3
    [Configuration.h, Configuration_adv.h, Menu Plans.xlsx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]
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2016-03-10 widen main frame
    widen main frame, still needs Z travel confirmed
    [bart pro xl top cross and frame v6.dxf]
2016-03-13 fixed X idler file name
    [bart x carriage.obj, bart x idler narrowed.stl, bart xl x carriage no zip tie.dxf]
2016-03-16 mod for 2 hole y clip
    2 hole y clip for 10 mm y rods also mod ends
    [bart pro xl y clip 2 hole.stl, bart pro xl y clip v2.f3d, bart xl end front lm10uu v2.dxf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]
2016-03-16 update Y motor mount
    fixed nut trap sizes, made main body thicker, added fillets
    [bart pro xl y motor mount v3 .f3d, bart pro xl y motor mount v3.stl]
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2016-03-19 update x axis lm10uu parts
    added no zip tie x carriage
    mod to motor end and idler end
    [bart pro xl lm10 X idler end v13.stl, bart pro xl lm10 X idler end.stl, bart pro xl lm10 X motor end v11.f3d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]
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2016-03-20 clean out deprecated files
    get rid of .step, obj and dxf files from printed parts source dir
    [bart x carriage.obj, bart xl x carriage no zip tie.dxf]
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2016-03-22 un nest z frame
    removed the z top and other z parts from the drawing to their own
    drawings
    [bart pro xl z frame v7.dxf]
2016-03-28 bed probe circuit
    voltage divider for bed probe circuit 24 volts to 5 volts
    [auxblox.GBL, auxblox.GBO, auxblox.GBP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]
2016-03-28 bed probe bracket v1
    stl and source for bed probe bracket
    [bart pro xl bed probe bracket.f3d, bart pro xl bed probe bracket.stl]
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2016-04-03 bed probe firmware settings
    changed settings for bed probe
    renamed file for mechanical z end stop
    updated readme
    [Configuration_mechanical_z.txt]
2016-04-03 update y motor mount
    update nut traps
    update slots for belt adjustment
    thicker mount
    [bart Y motor mount v2 .f3d, bart pro xl y motor mount v3 .f3d, bart pro xl y motor mount v3.stl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]
2016-04-03 push 1st rev of 2nd gen extruder
    2nd gen extruder and idler stl and source
    [bart pro xl 2nd gen extruder idler.stl, bart pro xl 2nd gen extruder.f3d, bart pro xl 2nd gen extruder.stl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]
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2016-04-09 config settings
    adjust bed probe distance
    disable bed runaway
    [Configuration.h]
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2016-04-17 update titan x carriage and mount
    second prototype of both parts
    [bart pro xl titan bracket.stl, bart pro xl titan x carriage.stl]
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2016-04-24 add steps per mm for lead screws in firmware
    [Configuration.h]
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2016-04-24 1st rev of m10 z and lead screw parts
    1st rev of m10 z rods and m8 lead screws
    x motor end
    x idler end
    no x idler at this point
    removed older m8 rod parts
    [bart pro xl all lm10uu Y idler end v11.f3d, bart pro xl all lm10uu Y idler end v11.stl, bart pro xl all m10 x motor end v10.f3d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]
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2016-04-24 2nd rev of 2nd gen extruder
    adjusted tensioner centerline
    slotted tensioner screw holes
    fixed e3d mount
    [bart pro xl 2nd gen extruder idler.stl, bart pro xl 2nd gen extruder v6.f3d, bart pro xl 2nd gen extruder v6.stl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]
2016-04-24 updated lead screw motor mounts
    adjusted spacing for z top and z motor mounts for m10 rods and lead
    screws
    [z lead scew frame top.dxf, z lead screw motor mounts.dxf]
2016-04-24 add m10 rod and lead screw main plate
    [z lead screw main upright.dxf]
2016-04-26 refinements to 2nd gen extruder
    larger hot end mount hole
    changed alignment of idler bearing to hob
    [bart pro xl 2nd gen extruder v6.f3d, bart pro xl 2nd gen extruder v6.stl, bart pro xl 2nd gen extruder v9.f3d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]
2016-04-26 refinements to m10 lead screw x parts
    strengthen x end stop mount
    thicker z bearing mount walls
    re profile x idler end
    addressed clearance issues with x idler
    [bart pro xl all lm10uu Y idler end v11.f3d, bart pro xl all m10 x motor end v10.f3d, bart pro xl lm10uu X idler end v25.f3d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]
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2016-06-09 change resistors to 0805 package
    changed package on r1 and r2, update mom and berbers
    [auxblox.brd, auxblox.sch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]
